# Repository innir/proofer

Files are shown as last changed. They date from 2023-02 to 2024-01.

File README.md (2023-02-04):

# Temperature control with timer for a homemade proofing box

## BOM

- LOLIN D1 mini (Pro)
- SSR RP1A23D5
- Power supply IRM-05-5
- Resistor 4.7 kOhm
- Terminal WAGO 250-202
- Terminal WAGO 250-203
- Housing GEH KSW 50 (G086)
- Temperature sensor DS18B20

- Heating cable / mat, 230V, ~20W
- Insulation box

## LICENSE

The project is licensed under the GNU LESSER GENERAL PUBLIC LICENSE 2.1. Files in the folder `kicad` are licensed under the Creative Commons Attribution-ShareAlike 4.0 International License (CC BY-SA). Files in the folder `kicad/snapeda-libraries` are provided by [SnapEDA](https://www.snapeda.com) and are licensed under the Creative Commons Attribution-ShareAlike 4.0 International License (CC BY-SA) with the [Design Exception 1.0](https://www.snapeda.com/about/FAQ/#designexception).

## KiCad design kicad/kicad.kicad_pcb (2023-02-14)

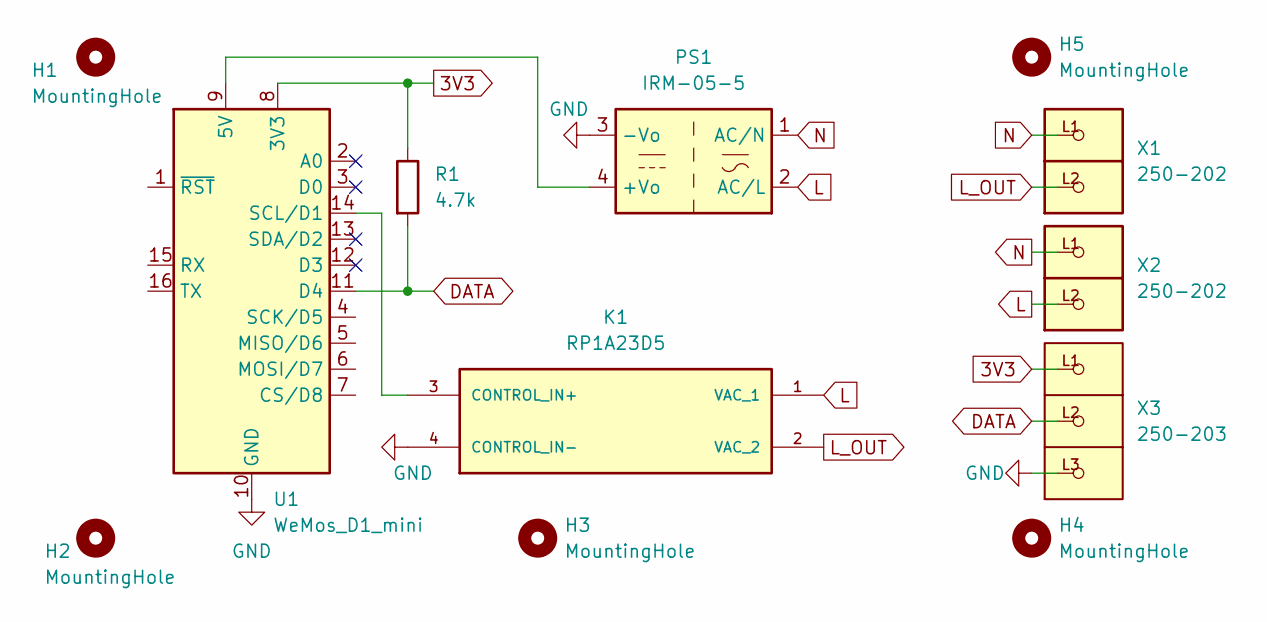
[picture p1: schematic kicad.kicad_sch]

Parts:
H1, H2, H3, H4, H5: MountingHole; MountingHole_2.7mm_M2.5
K1: RP1A23D5; RELAY_RP1A23D5; PARTREV 30/08/2021
PS1: IRM-05-5; Converter_ACDC_MeanWell_IRM-05-xx_THT
R1: 4.7k; R_Axial_DIN0207_L6.3mm_D2.5mm_P10.16mm_Horizontal
U1: WeMos_D1_mini; WEMOS_D1_mini_light
X1, X2: 250-202; P-250-202
X3: 250-203; P-250-203

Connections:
3V3: R1.1, U1.8 (3V3), X3.L1
DATA: R1.2, U1.11 (D4), X3.L2
GND: K1.4 (CONTROL_IN-), PS1.3 (-Vo), U1.10 (GND), X3.L3
L: K1.1 (VAC_1), PS1.2 (AC/L), X2.L2
L_OUT: K1.2 (VAC_2), X1.L2
N: PS1.1 (AC/N), X1.L1, X2.L1
unnamed: K1.3 (CONTROL_IN+), U1.14 (SCL/D1)
unnamed: PS1.4 (+Vo), U1.9 (5V)

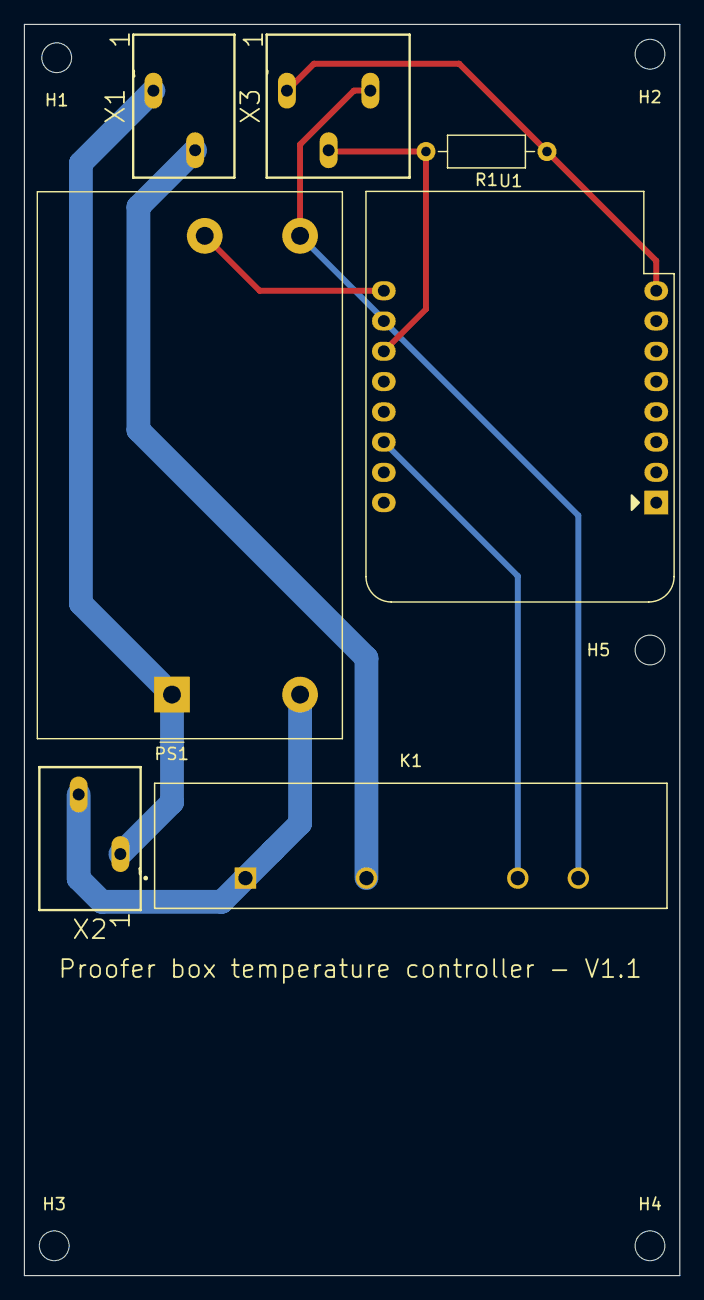
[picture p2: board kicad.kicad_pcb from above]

Board: 2 copper layers, 55.0 x 105.0 mm, 12 parts (0 on the bottom side), 8 nets.

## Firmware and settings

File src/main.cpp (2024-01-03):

#include <Arduino.h>
#include <ArduinoOTA.h>
#include <ESPAsyncWebServer.h>
#include <FS.h>
#include <LittleFS.h>
// Set your time zone (on ESP8266, see TZ.h for available time zones)
#ifdef ESP32
#define TZ PSTR("CET-1CEST,M3.5.0,M10.5.0/3")
#else
#include <TZ.h>
#define TZ TZ_Europe_Berlin
#endif
#include <ctime>
#include <tempProbe.h>

// No mDNS for OTA updates
#define NO_GLOBAL_MDNS

// Pin to control the relay is D1
#ifdef ARDUINO_LOLIN_C3_MINI
#define D1 10
#endif
#define RELAY_PIN D1

// Control heating every 10 seconds
#define UPDATE_INTERVAL_MS 10000

// Offset to compensate for the inertia of the heating system [°C]
#define THERMAL_OFFSET 0.2

// Update csv once a minute
#define CSV_UPDATE_INTERVAL_MS 60000

float sTemp = 21.0;
float cTemp = 0.0;
bool isSystemOn = false;
bool isHeating = false;
bool prevHeatingState = false;
std::tm proofEnd = {};

uint64_t previousMillis = 0;
uint64_t csv_previousMillis = 0;

File csv;

AsyncWebServer server(80);

String getTime() {
  time_t now = std::time({});
  char timeString[sizeof("yyyy-mm-dd hh:mm:ss")];
  std::strftime(timeString, sizeof(timeString), "%F %T", std::localtime(&now));
  return String(timeString);
}

void writeCSV() {
  String text = getTime() + "," + String(cTemp) + "," +
                (isSystemOn ? String((int)isHeating) : "");
  csv.println(text);
  csv.flush();
}

void handleSetpoint(AsyncWebServerRequest *request) {
  if (request->method() == HTTP_POST) {
    if (!request->hasParam("value")) {
      request->send(400, "text/plain", "Invalid Request");
      return;
    }
    sTemp = (request->getParam("value")->value()).toFloat();
    request->send(200, "text/plain",
                  "OK: Temperature set to " + String(sTemp) + "°C");
  } else if (request->method() == HTTP_GET) {
    request->send(200, "text/plain", String(sTemp));
  }
}

void handleSytemState(AsyncWebServerRequest *request) {
  if (request->method() == HTTP_POST) {
    if (!request->hasParam("value")) {
      request->send(400, "text/plain", "Bad Request");
      return;
    }
    String val = request->getParam("value")->value();
    if (val.equalsIgnoreCase("on")) {
      isSystemOn = true;
    } else if (val.equalsIgnoreCase("off")) {
      isSystemOn = false;
    } else {
      request->send(400, "text/plain", "Bad Request");
      return;
    }
    request->send(200, "text/plain",
                  "OK: System is switched " +
                      String(isSystemOn ? "on" : "off"));
  } else if (request->method() == HTTP_GET) {
    request->send(200, "text/plain", String(isSystemOn ? "on" : "off"));
  }
}

void handleProofEnd(AsyncWebServerRequest *request) {
  if (request->method() == HTTP_POST) {
    if (!request->hasParam("value")) {
      request->send(400, "text/plain", "Bad Request");
      return;
    }
    char val[sizeof("yyyy-mm-ddThh:mm:ss")];
    request->getParam("value")->value().toCharArray(val, sizeof(val));
    strptime(val, "%FT%T", &proofEnd);
    request->send(200, "text/plain", "OK: Proofing end set");
  } else if (request->method() == HTTP_GET) {
    char timeString[sizeof("yyyy-mm-ddThh:mm:ss")];
    std::strftime(timeString, sizeof(timeString), "%FT%T", &proofEnd);
    request->send(200, "text/plain", String(timeString));
  }
}

void setup(void) {
  Serial.begin(115200);

  // Initialize LittleFS
  if (!LittleFS.begin()) {
    Serial.println("Could not initialize LittleFS");
    return;
  }

  // Configure pin to control the relay
  pinMode(RELAY_PIN, OUTPUT);

  // Get WiFi credentials
  File cred = LittleFS.open("/cred.conf", "r");
  String tmp = cred.readStringUntil('\n');
  char ssid[tmp.length() + 1];
  tmp.toCharArray(ssid, sizeof(ssid));
  tmp = cred.readStringUntil('\n');
  char password[tmp.length() + 1];
  tmp.toCharArray(password, sizeof(password));
  cred.close();

  // Connect to WiFi
  WiFi.begin(ssid, password);
  while (WiFi.status() != WL_CONNECTED) {
    Serial.println("Connecting to WiFi...");
    delay(5000);
  }

  // Print IP address
  Serial.print("IP Address: ");
  Serial.println(WiFi.localIP());

  // Start NTP server
  configTzTime(TZ, "pool.ntp.org");
  yield();
  // Let's wait up to one minute to get a NTP sync
  while (std::time({}) <= 60) {
    Serial.println("Waiting for NTP sync...");
    delay(2000);
    yield();
  }
  Serial.println("Got NTP sync, it's " + getTime());

  // Set up OTA
  ArduinoOTA.onStart([]() {
    String type;
    if (ArduinoOTA.getCommand() == U_FLASH) {
      type = "sketch";
    } else {
      type = "filesystem";
      // Unmount FS before updating
      LittleFS.end();
    }
    Serial.println("Start updating " + type);
  });

  ArduinoOTA.onEnd([]() { Serial.println("OTA update finished"); });

  ArduinoOTA.onError([](ota_error_t error) {
    (void)error;
    Serial.println("OTA update failed");
  });

  ArduinoOTA.begin();

  // Set up temp probe
  setupTempProbe();

  // Read temperature
  cTemp = getTemp();

  // Open log file
  csv = LittleFS.open("/data.csv", "w");

  // Write csv header and first log
  csv.println("Time,Temp,Heater");
  writeCSV();

  // Handle API calls
  server.on("/systemState", handleSytemState);
  server.on("/setpoint", handleSetpoint);
  server.on("/proofEnd", handleProofEnd);

  // Serve static files
  server.serveStatic("/data.csv", LittleFS, "/data.csv")
      .setCacheControl("max-age=0");
  server.serveStatic("/", LittleFS, "/www/")
      .setCacheControl("max-age=86400")
      .setDefaultFile("index.html");

  server.onNotFound([](AsyncWebServerRequest *request) {
    request->send(404, "text/plain", "Not Found");
  });

  // Set proofing end to now
  time_t now = std::time({});
  proofEnd = *std::localtime(&now);

  server.begin();
}

void loop(void) {
  ArduinoOTA.handle();

  uint64_t currentMillis = millis();
  if (currentMillis - csv_previousMillis >= CSV_UPDATE_INTERVAL_MS) {
    csv_previousMillis = currentMillis;
    cTemp = getTemp();
    writeCSV();
    Serial.println(
        getTime() + ": System is " + String(isSystemOn ? "on" : "off") +
        ", heater is " + String(isHeating ? "on" : "off") + ", temp is " +
        String(cTemp) + "°C" + " and setpoint is " + String(sTemp) + "°C");
  }

  currentMillis = millis();
  if (currentMillis - previousMillis >= UPDATE_INTERVAL_MS) {
    previousMillis = currentMillis;
    prevHeatingState = isHeating;
    if (std::mktime(&proofEnd) <= std::time({})) {
      isSystemOn = false;
    }
    if (isSystemOn) {
      cTemp = getTemp();
      if (cTemp < sTemp - THERMAL_OFFSET) {
        isHeating = true;
      } else if (cTemp >= sTemp - THERMAL_OFFSET) {
        isHeating = false;
      }
    } else {
      isHeating = false;
    }
    if (prevHeatingState != isHeating) {
      digitalWrite(RELAY_PIN, isHeating);
      writeCSV();
    }
  }
}

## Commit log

2023-01-30 Add timer to set proofing end
2023-02-03 Use offset instead of alowance to control temperature
2023-02-03 Use correct unsigned integer type
    [main.cpp]
2023-02-04 Add schematic, footprint and a short readme
    [kicad.kicad_pcb, kicad.kicad_sch]
2023-02-10 Ignore some kicad cache files
2023-02-12 Small schematic & footprint cleanups
    [kicad.kicad_pcb, kicad.kicad_sch]
2023-02-14 WIP: some more schematic & footprint updates
    [kicad.kicad_pcb, kicad.kicad_sch]
